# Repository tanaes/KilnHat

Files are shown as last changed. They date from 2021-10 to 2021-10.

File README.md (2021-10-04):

# KilnHat
PCB for running a kiln from a Raspberry Pi.

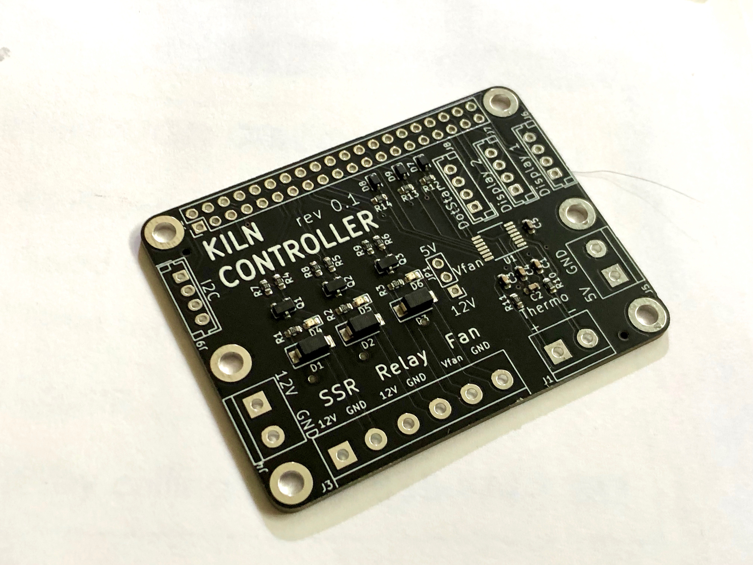
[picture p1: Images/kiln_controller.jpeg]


Has three MOSFET channels for controlling a mechanical safety relay, an SSR, and a fan. On-board thermocouple amplifier. Includes outputs for digital displays, addressable LEDs, and an I2C port.

*This is not yet a true 'hat' as I haven't yet implemented the full requirements!* However, my goal is to test the initial prototypes and add the required I2C EEPROM and over-voltage protection circuitry in a subsequent revision.

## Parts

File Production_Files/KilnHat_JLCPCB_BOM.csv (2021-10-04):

Comment | Designator | Footprint | LCSC Part #
.01uF Unpolarized capacitor, small symbol | C1,C3 | C_0603_1608Metric | 0603
.1uF Unpolarized capacitor, small symbol | C2,C4,C5 | C_0603_1608Metric | C14663
D_Schottky Schottky diode | D1,D2,D3 | D_SMA | C22452
LED Light emitting diode | D4,D5,D6 | LED_0603_1608Metric | C2286
1N4148WS 75V 0.15A Fast switching Diode, SOD-323 | D7,D8,D9 | D_SOD-323 | C2128
AO3400A 50V Vds, 0.22A Id, N-Channel MOSFET, SOT-23 | Q1,Q2,Q3 | SOT-23 | C20917
4.7k Resistor | R1,R2,R3 | R_0603_1608Metric | C23162
100 Resistor | R4,R5,R6,R10,R11 | R_0603_1608Metric | C22775
10k Resistor | R7,R8,R9,R12,R13,R14 | R_0603_1608Metric | C25804

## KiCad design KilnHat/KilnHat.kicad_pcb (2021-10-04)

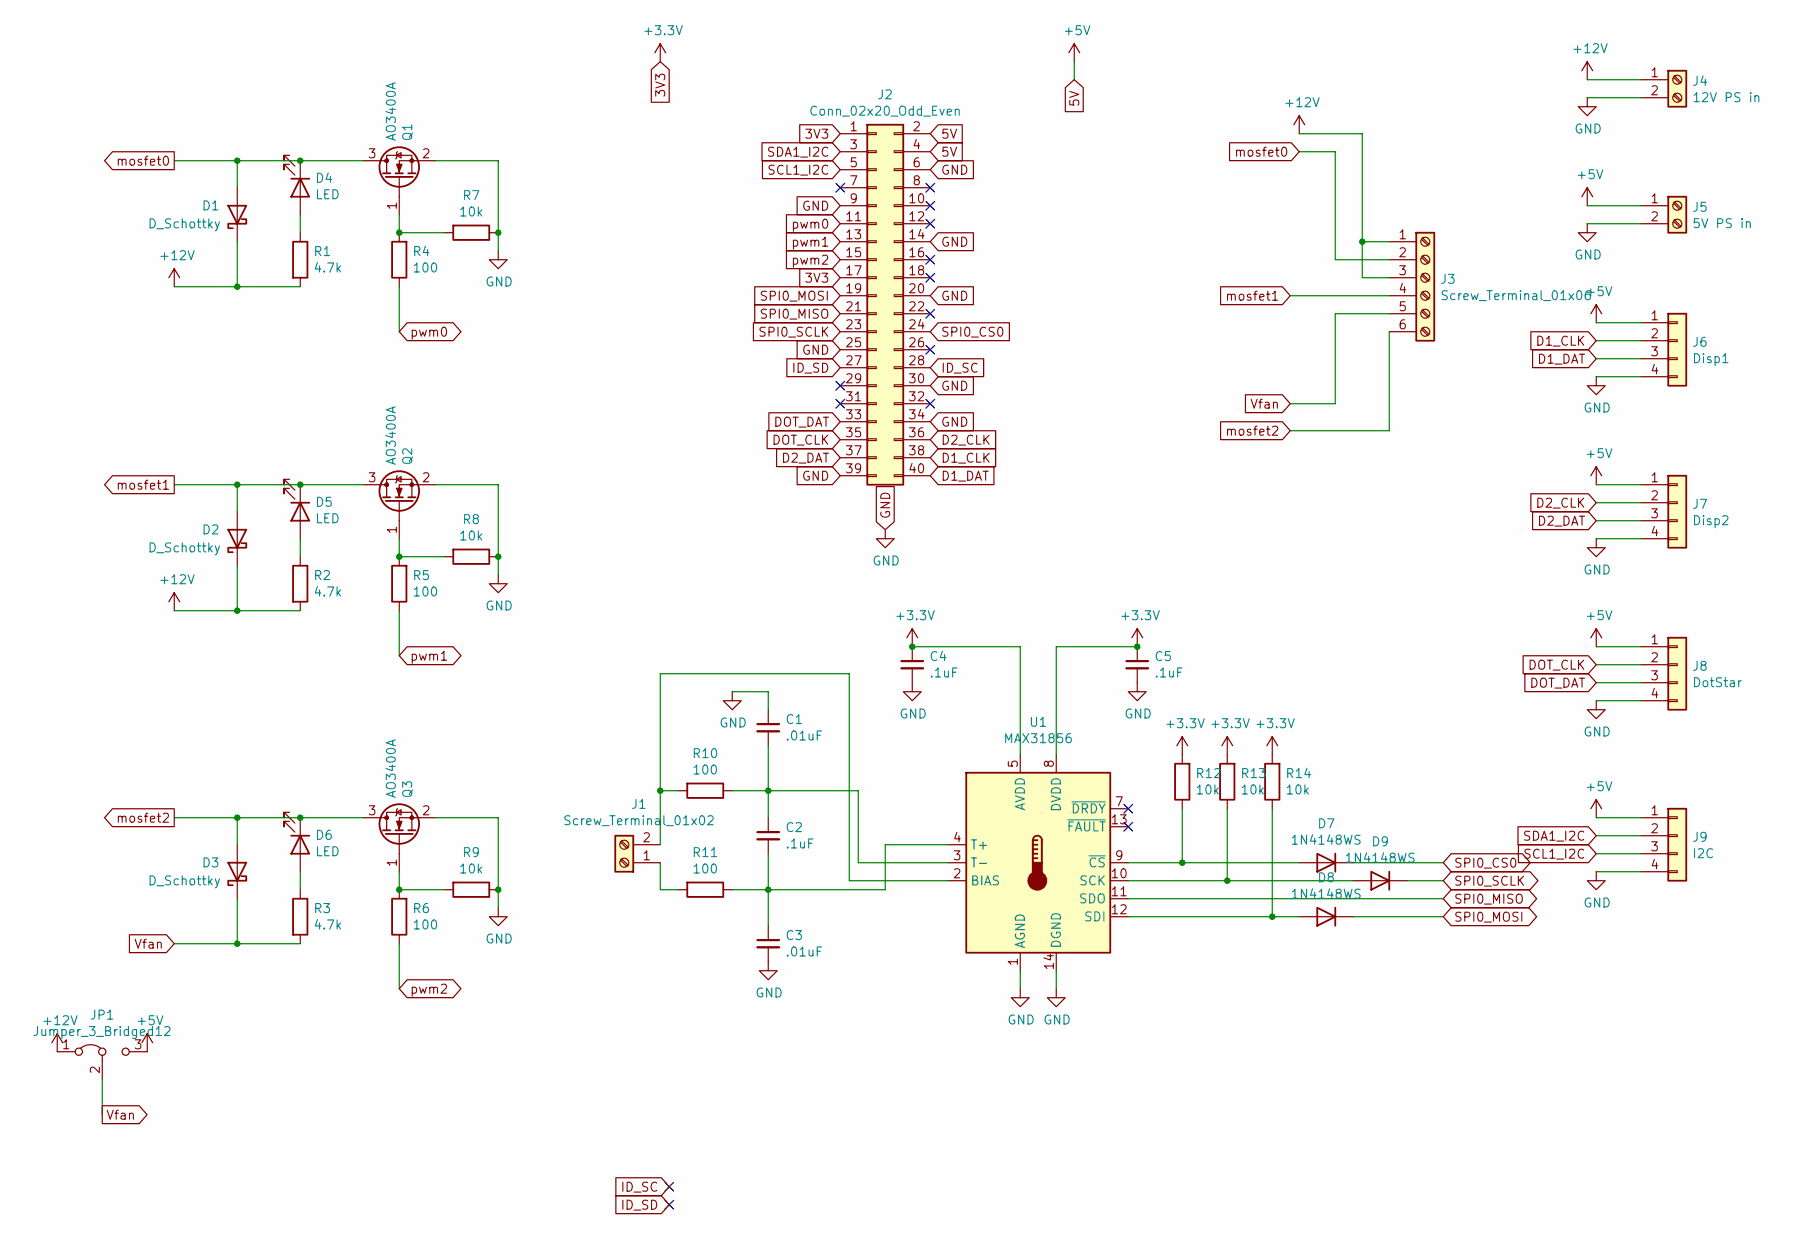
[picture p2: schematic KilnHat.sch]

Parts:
C1, C3: .01uF; C_0603_1608Metric; JLCPCB BOM 1
C2, C4, C5: .1uF; C_0603_1608Metric; JLCPCB BOM 1
D1, D2, D3: D_Schottky; D_SMA; JLCPCB BOM 1
D4, D5, D6: LED; LED_0603_1608Metric; JLCPCB BOM 1
D7, D8, D9: 1N4148WS; D_SOD-323; JLCPCB BOM 1
J1: Screw_Terminal_01x02; TerminalBlock_bornier-2_P5.08mm; JLCPCB BOM 0
J2: Conn_02x20_Odd_Even; PinHeader_2x20_P2.54mm_Vertical; JLCPCB BOM 0
J3: Screw_Terminal_01x06; TerminalBlock_bornier-6_P5.08mm; JLCPCB BOM 0
J4: 12V PS in; TerminalBlock_bornier-2_P5.08mm; JLCPCB BOM 0
J5: 5V PS in; TerminalBlock_bornier-2_P5.08mm; JLCPCB BOM 0
J6: Disp1; JST_EH_B4B-EH-A_1x04_P2.50mm_Vertical; JLCPCB BOM 0
J7: Disp2; JST_EH_B4B-EH-A_1x04_P2.50mm_Vertical; JLCPCB BOM 0
J8: DotStar; JST_EH_B4B-EH-A_1x04_P2.50mm_Vertical; JLCPCB BOM 0
J9: I2C; JST_EH_B4B-EH-A_1x04_P2.50mm_Vertical; JLCPCB BOM 0
JP1: Jumper_3_Bridged12; PinHeader_1x03_P2.54mm_Vertical; JLCPCB BOM 0
Q1, Q2, Q3: AO3400A; SOT-23; JLCPCB BOM 1
R1, R2, R3: 4.7k; R_0603_1608Metric; JLCPCB BOM 1
R4, R5, R6, R10, R11: 100; R_0603_1608Metric; JLCPCB BOM 1
R7, R8, R9, R12, R13, R14: 10k; R_0603_1608Metric; JLCPCB BOM 1
U1: MAX31856; TSSOP-14_4.4x5mm_P0.65mm; JLCPCB BOM 0

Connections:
3V3: C4.1, C5.1, J2.1, J2.17, R12.2, R13.2, R14.2, U1.5 (AVDD), U1.8 (DVDD)
5V: J2.2, J2.4, J5.1, J6.1, J7.1, J8.1, J9.1, JP1.3 (B)
+12V: D1.1 (K), D2.1 (K), J3.1, J3.3, J4.1, JP1.1 (A), R1.2, R2.2
D1_CLK: J2.38, J6.2
D1_DAT: J2.40, J6.3
D2_CLK: J2.36, J7.2
D2_DAT: J2.37, J7.3
DOT_CLK: J2.35, J8.2
DOT_DAT: J2.33, J8.3
GND: C1.1, C3.2, C4.2, C5.2, J2.6, J2.9, J2.14, J2.20, J2.25, J2.30, J2.34, J2.39, J4.2, J5.2, J6.4, J7.4, J8.4, J9.4, Q1.2 (S), Q2.2 (S), Q3.2 (S), R7.1, R8.1, R9.1, U1.1 (AGND), U1.14 (DGND)
ID_SC: J2.28
ID_SD: J2.27
unnamed: C1.2, C2.1, R10.1, U1.3 (T-)
unnamed: C2.2, C3.1, R11.1, U1.4 (T+)
unnamed: D4.2 (A), R1.1
unnamed: D5.2 (A), R2.1
unnamed: D6.2 (A), R3.1
unnamed: D7.2 (A), R12.1, U1.9 (~CS)
unnamed: D8.2 (A), R14.1, U1.12 (SDI)
unnamed: D9.2 (A), R13.1, U1.10 (SCK)
unnamed: J1.1, R11.2
unnamed: J1.2, R10.2, U1.2 (BIAS)
unnamed: Q1.1 (G), R4.2, R7.2
unnamed: Q2.1 (G), R5.2, R8.2
unnamed: Q3.1 (G), R6.2, R9.2
SCL1_I2C: J2.5, J9.3
SDA1_I2C: J2.3, J9.2
SPI0_CS0: D7.1 (K), J2.24
SPI0_MISO: J2.21, U1.11 (SDO)
SPI0_MOSI: D8.1 (K), J2.19
SPI0_SCLK: D9.1 (K), J2.23
Vfan: D3.1 (K), J3.5, JP1.2 (C), R3.2
mosfet0: D1.2 (A), D4.1 (K), J3.2, Q1.3 (D)
mosfet1: D2.2 (A), D5.1 (K), J3.4, Q2.3 (D)
mosfet2: D3.2 (A), D6.1 (K), J3.6, Q3.3 (D)
pwm0: J2.11, R4.1
pwm1: J2.13, R5.1
pwm2: J2.15, R6.1

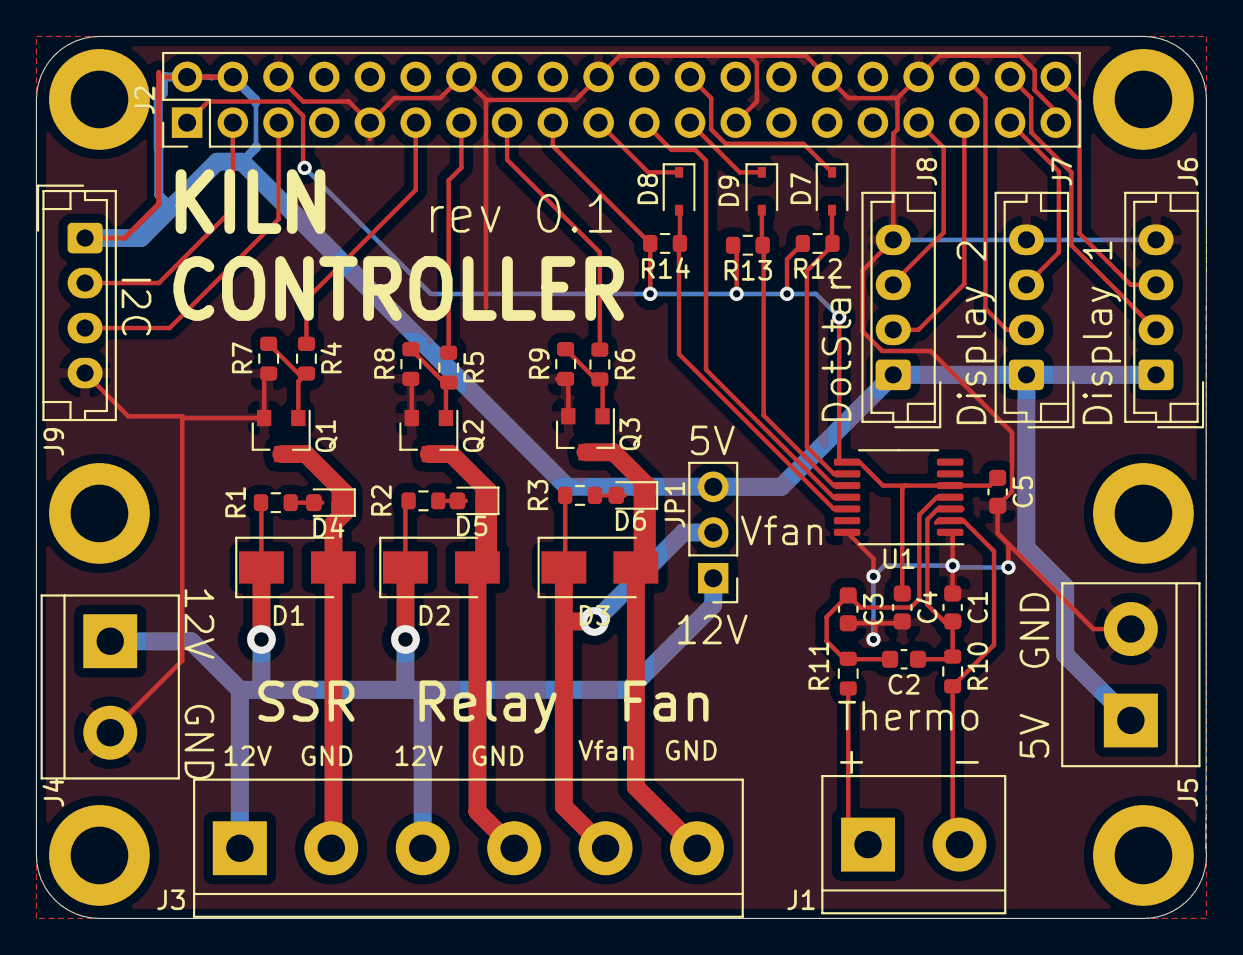
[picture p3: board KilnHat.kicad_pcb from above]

Board: 2 copper layers, 65.0 x 49.0 mm, 42 parts (0 on the bottom side), 36 nets.
